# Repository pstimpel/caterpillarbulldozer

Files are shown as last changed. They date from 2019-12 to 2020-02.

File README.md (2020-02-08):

# Caterpillar bulldozer
3D printed radio controlled bulldozer, 2 feet long

License: https://creativecommons.org/licenses/by-nc-sa/4.0/

Most obvious limits of this license:
- You are not allowed to use this stuff for commercial purposes
- You can download, reupload and change the stuff, but have to release it under the same license again
- You have the mention the origin, "Original by Peter Stimpel, https://github.com/pstimpel/caterpillarbulldozer/"

## Home of this project

https://github.com/pstimpel/caterpillarbulldozer/

### Other ressources

- Thingiverse: https://www.thingiverse.com/thing:4057714
- Prusaprinters.org: https://www.prusaprinters.org/prints/15078-caterpillar-bulldozer-rc
- Pinshape: https://pinshape.com/items/57510-3d-printed-caterpillar-bulldozer-rc

IMAGE ALT TEXT HERE (https://www.youtube.com/watch?v=pU6fe7RiBuI)

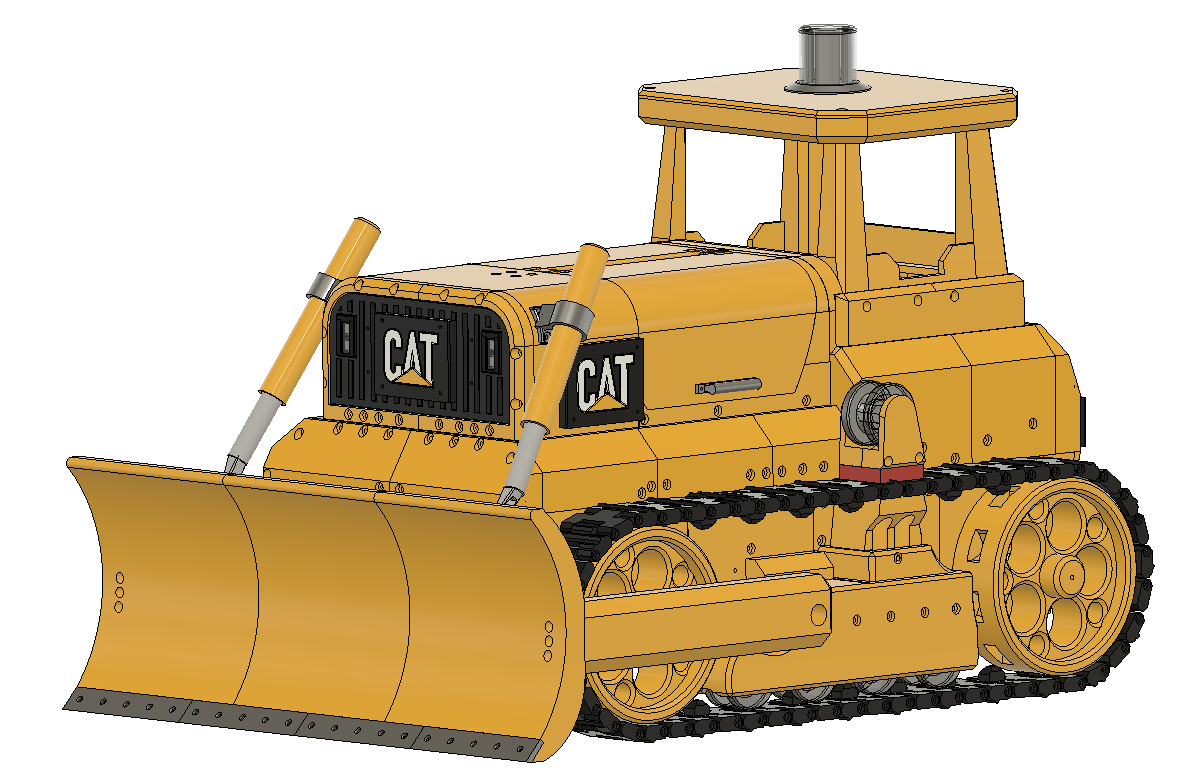
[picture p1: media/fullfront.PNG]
In all its glory


**Table of contents**
* [What's the story?](#what-s-the-story-)
* [A bulldozer!](#a-bulldozer-)
* [Sourcing parts, what do we need](#sourcing-parts--what-do-we-need)
+ [Filament, print instructions](#filament--print-instructions)
+ [Candy](#candy)
+ [Bearings](#bearings)
+ [Screws, nuts and bolts](#screws--nuts-and-bolts)
    - [M2](#m2)
    - [M3](#m3)
    - [M4](#m4)
+ [Electronics](#electronics)
    - [RC stuff](#rc-stuff)
    - [stuff for lights and buzzer](#stuff-for-lights-and-buzzer)
    * [Stuff to create a pcb](#stuff-to-create-a-pcb)
* [Let's build the bullozer now](#let-s-build-the-bullozer-now)
* [Who to thank?](#who-to-thank-)
* [Donation](#donation)
* [Feedback](#feedback)

## What's the story?

I run my hobby 3d printing for more than a year now. Yes, I am a noob. Along the way I looked for a software to do my CAD, and found Fusion 360 from Autodesk. So, I had to learn Fusion. Youtube offers great ressources, most important there is the Fusion 360 channel run by Autodesk (https://www.youtube.com/user/AutodeskFusion360). There is a bunch of lovely people with their tips and tricks - more details at the end of this. 

However, one day - I was finishing my illuminated death star (https://www.prusaprinters.org/prints/5661-death-star-illuminated-mood-lamp-death-star ), I was looking for a thing taking more than a few days to create. Something to be my project for the winter. And, I was keen to create something running on tracks. Now I dislike building replicas of war machinery, so a tank was no solution to me. 

## A bulldozer!

I was using my favorite search engine duck duck go, and found Caterpillar to be a big brand in the bulldozer manufacturers community. I sat down and thought what to do, and came up with these topics:

- no real replica, more a free style model of a bulldozer
- dimensions? who cares!
- radio controlled, and not steered by a gearbox, but two motors (I liked the challenge of learning how to program my radio control)
- the blade at the front should move up and down by servo motors

But how the f*** could I achieve these goals? I decided to create a gearbox first, add the motors to a motor stand, so I could test if running two independent tracks by an own motor each would be a cool thing. 

And what to tell: doing gears is easy enough in Fusion. I added some bearings, adjusted the tolerances, and had a working gearbox a few hours later. I mirrored it, added some dirty housing around, and created a design for the tracks.

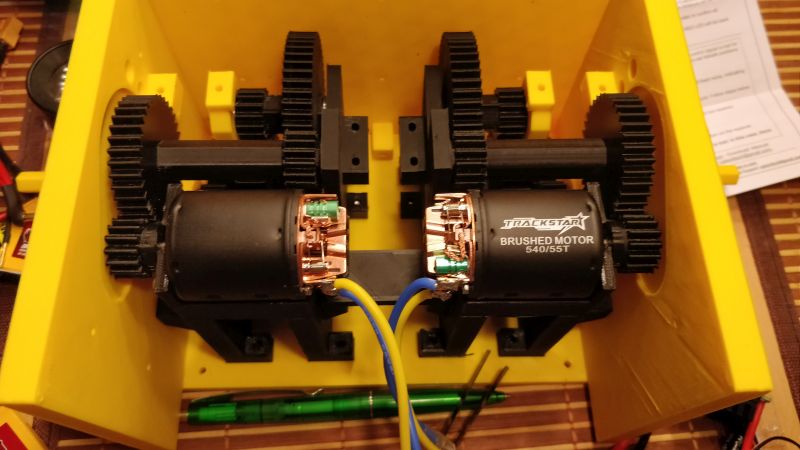
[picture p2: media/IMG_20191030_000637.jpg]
First revision of the gearbox


Stearing two tracks having a motor each was not as easy as I thought. But the guys at (https://openrcforums.com) helped me out, so I got my radio control running quite soon. 

Next step: tracks. I designed a track in Fusion, printed the parts, screwed it together and started a very first test. This was the beginning of this story.

Video of the first test: 

IMAGE ALT TEXT HERE (https://www.youtube.com/watch?v=s0oiE-nRtp8)

Now, how to go on? Usually, you would design all the stuff, and once you are happy with your CAD, you print and assemble the stuff. I was going a different way. I designed the stuff during building the vehicle. Step by step both the CAD and the vehicle evolved. This caused some major mistakes and lot's of fun at the same time. I love it that way - CHAOS! One thing that was quite tough: you had to think about the next step, one step ahead, so you can connect the two steps somehow. Thank the lord there is candy ...

## Sourcing parts, what do we need

We need a 3d printer. I was using my Prusa I3 MK3. It has a build plate of 200x250, and Z is 200+. Some parts make use of these dimensions. If your printer has less build area, this project might not be for you, or you need to cut things apart. Of course we need tools. And, we need ...

### Filament, print instructions

I was using filament from my favorite supplier https://dasfilament.de. The print is PLA only, so I ordered about

- 6 spools yellow
- 1 spool transparent
- 2 spools black
- 1 spool anthracite
- 1 spool silver
- 1 spool white

Numbers are valid for printing in 0.3 layer height, using 3 shells horizontally and vertically, 10% cubic infill (except the gears and axles, I used 50% cubic infill here).

I was taking care not to need any support. I achieved this goal, except for very few parts.

The stls are not in their orientation for hassle free printing, I'm sorry. You do need to make this yourself in your slicer.

**Update upon user request**: If you find 3mf files to be more convinient to print, you might want to look at the folder "3mf-200x250". It contains 59 3mf-files. The orientation of the parts to print is set there already, also the numbers of parts to print is the right one already. To use these files your slicer has to support 3mf. Each of these files contains a full organized print bed, made for print beds equal to or larger than 200x250mm in dimension. Each filename is led by a number, which represents the order you should print the files. It contains as well an information for the filament color to use. "nocolor" means you can use a color of your choice since the files are hidden inside your bulldozer. 

### Candy

The build will take some time, not to talk about the 200 hours of printing. This means, it will be nerve-wracking :). Get some good stock of candy to please yourself once you enter mentally strange situations. I can tell you: you will need it!

### Bearings

We need 40 bearings of type 6700ZZ. Dimensions are 10x15x4mm. These are standard bearings, you should find them very easy. I ordered mine from https://www.kugellager-express.de/. 

We need another 12 bearings of type 6904 with dimensions 20x37x9mm. I ordered them from the same supplier.

### Screws, nuts and bolts

I order my stuff from a shop called https://www.schrauben-paul.com/. All given dimensions are mm. I did not count each single screw, so all numbers are estimates. However, if you enter such a project I expect you won't order exact counts.

#### M2
- 50 M2x8, cylinder head
- 50 M2x10, cylinder head
- 50 M2x16, cylinder head

#### M3
- 4 scrubscrews M3x6
- 4 square nuts M3
- 100 M3x10, cylinder head
- 100 M3x14, cylinder head
- 300 M3x20, cylinder head
- 100 M3x25, cylinder head
- 200 M3x45, cylinder head

#### M4
- 4 Bolts 40mm

### Electronics

I expect you have a radio control already. Therefore I do not link a receiver. But, you will need one 8 channel receiver matching your radio control and local laws. If you skip the lights part, a 4 channel receiver will do. As well, all my builds are ran by 2S Lipo, which means the voltage of the linked components below does match this battery type. If you go for a different voltage, please select your components in a way the match together.

#### RC stuff
- 2 standard servos, metal gear, metal servo arm (https://www.amazon.de/gp/product/B0716V3WNH/)
- 2 motors type 540, 55 turns or similar (https://hobbyking.com/de_de/1-10-540-carbon-brushed-motor-55t.html)
- 2 ESCs (https://hobbyking.com/de_de/hobbyking-x-car-45a-brushed-car-esc.html)
- 2 Lipo 2S, like (https://hobbyking.com/de_de/turnigy-nano-tech-shorty-4200mah-2s2p-65-130c-hardcase-lipo-pack-roar-approved.html)
- 2 connectors to connect your Lipos and ESCs

#### stuff for lights and buzzer
- Arduino Nano 5 Volt
- Resistor 0.25W 270 Ohm
- Buzzer 5 Volt (https://www.amazon.de/gp/product/B073RH8TQK/), we need the bigger one out of the package
- 1 switch like in (https://www.amazon.de/gp/product/B07MY2WVQ3)
- RGB leds (https://www.amazon.de/gp/product/B01N97A0XG)
- 3 cables for connecting receiver and Arduino, servo cables like (https://hobbyking.com/de_de/twisted-15cm-female-to-female-servo-lead-jr-22awg-10pcs-set.html)
- wires to connect the LEDs (https://www.amazon.de/gp/product/B01BI1G88C)
- 12 pin headers
- solder stuff, some shrinking tube 3mm

##### Stuff to create a pcb

We create a one sided, 60x60mm pcb. I expect you either have the stuff to do that because you know how to do it, or you just order the pcb from your favorite supplier. You can skip the pcb part completely, because it just controls the lights and the buzzer. If you do not need this, just order the rc stuff only. You could exchange your 8 channel receiver for a 4 channel receiver in this case as well.

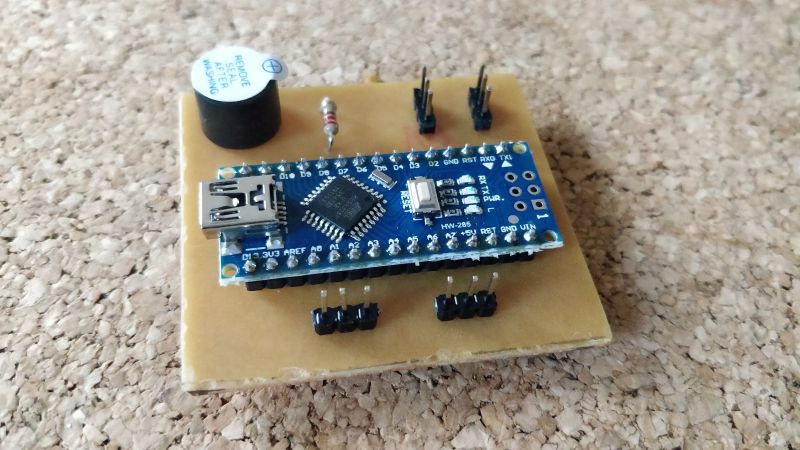
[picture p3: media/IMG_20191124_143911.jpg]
Arduino board


But hey, no lights? Really?

**Warning**: I have still issues with flickering, randomly color changing LEDs, seems there is some noise coming from the ESCs and I need to filter those out. It is very likely the pcb design and parts list of the pcb will change soon.

## Let's build the bullozer now

**Remark**: if not mentioned any different, we talk about screwing things together using M3 screws. Just screw them into the plastic parts, make sure not going to fast when screwing them in. Friction causes heat, and heat cause melted plastic parts. Just be gentle. Do not overtighten the screws, there is no need for it. It is on you to determine the right length of a srew, just use common sense and do not try to mount a small handle using M3x45. 

We start with the gear box. Print all items in subfolder "BothSides" twice. Print items in "Housing", "LeftOnly" and "RightOnly" once each. The gears and axles need to be stable. I suggest you to print the axles horizontally aligned. Use some more dense infill on the gears and axles. 

Mount the motorstands to the base. Assemble all axle-gear combinations twice, once for left and one for right gearbox. Take note of the indexed axles, and their counterpart gears. Most gears have one side flat, while the other has kind of a builtin spacer. The spacer side points outside the axle, to the bearing. Axles A, B and C provide spacer parts, which sit in the middle between the gears.

Axle A is the one right after the motor. Axle B "connects" to Axle A and Axle C and so on. Should be straight forward. Do not miss the 6700 bearings, one at each end of each axle. Except "rearaxle", we will take care of those later.

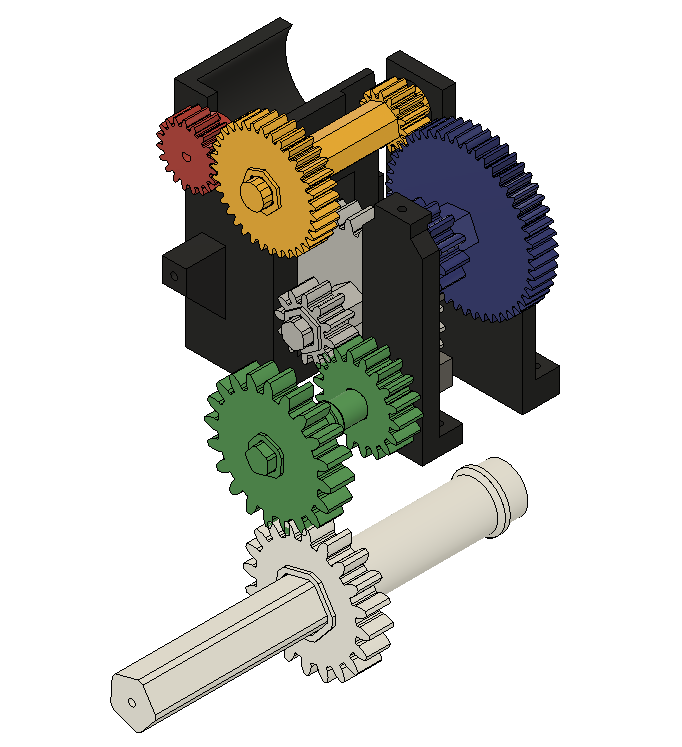
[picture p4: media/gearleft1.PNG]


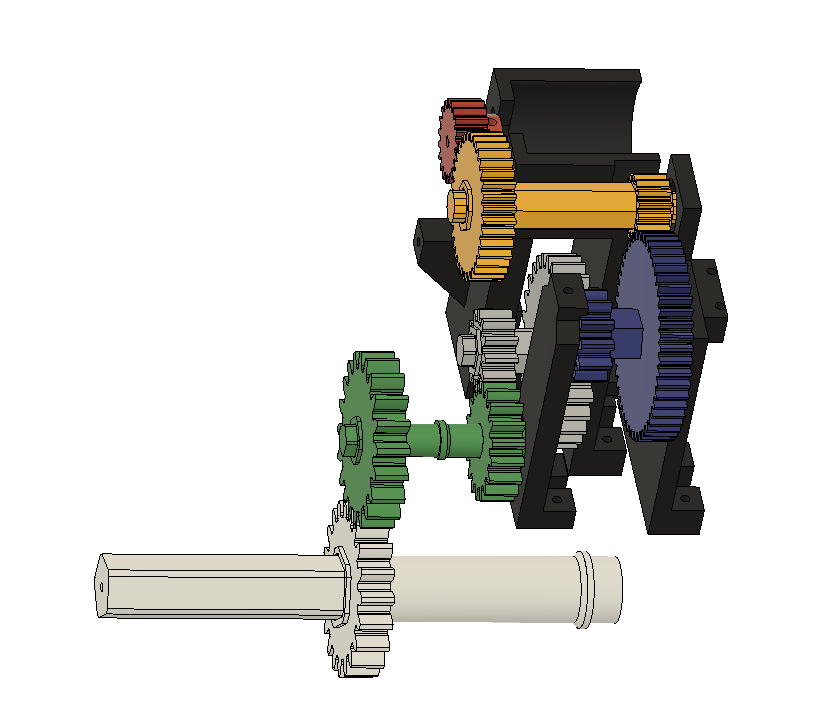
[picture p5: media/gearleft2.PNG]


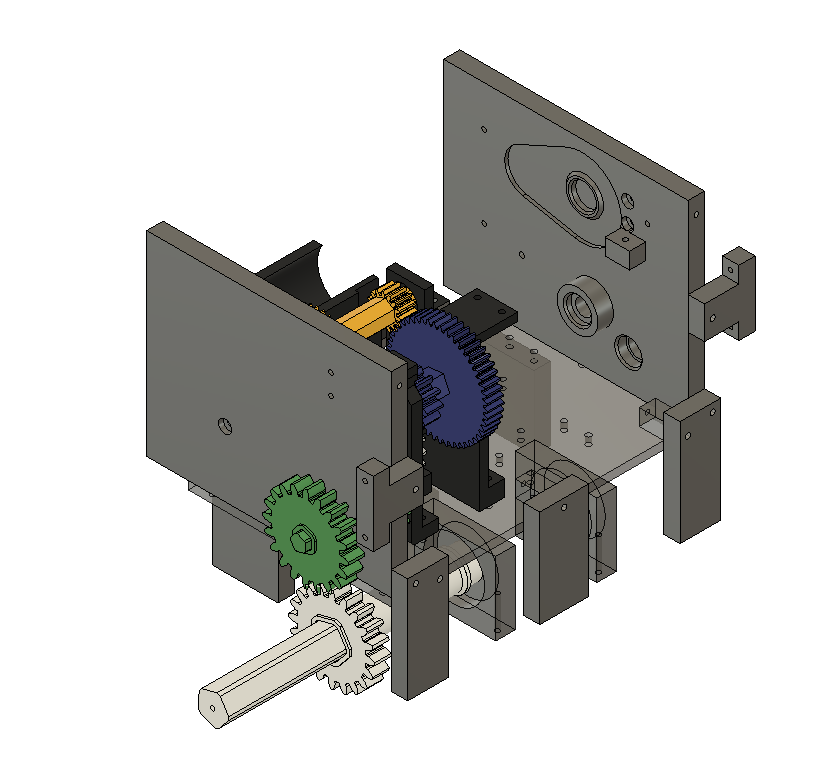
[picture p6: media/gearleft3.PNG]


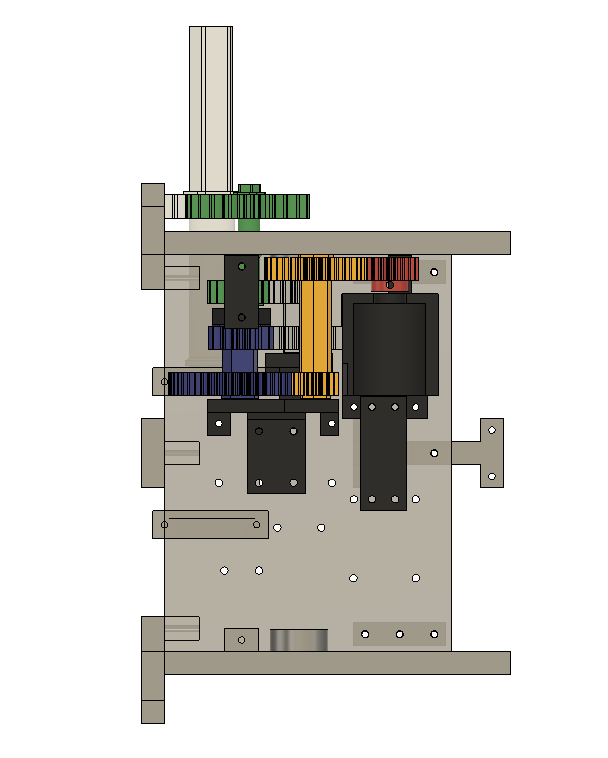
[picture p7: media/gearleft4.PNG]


Once all axles are assemnbled, use the "Gearboxbearingstands" to mount them at your gearbox base. Do this twice, for left and right gearset. Mount the outer housing "Gearhousing left/right". Make sure the gears can spin freely. Add the motors to the stands, fix them. The pinions are now mounted to your motors using 4 squarenuts and 4 scrubscrews M3. Add the supports and connector parts for Bearing holders and motorstands.

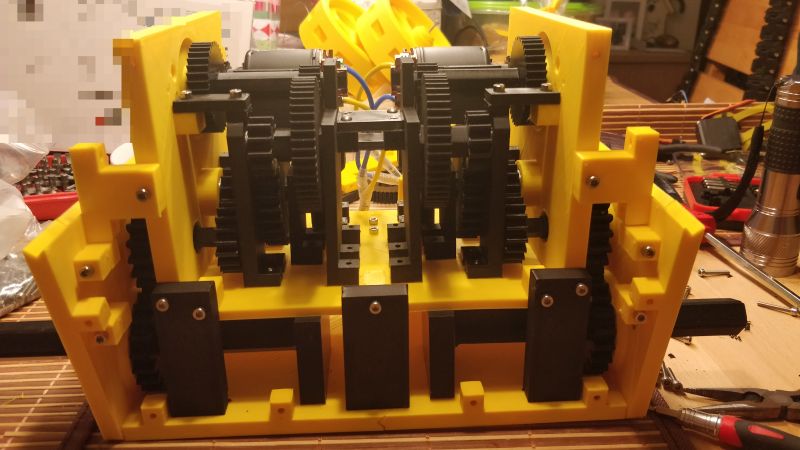
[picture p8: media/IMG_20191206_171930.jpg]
The gearbox, ready assembled and mounted to the chassis of the vehicle


This is a good time to connect ESCs to the motors, Lipos to the ESCs and the receiver to the ESCs - for a very first test. **WARNING: Remove one of the positive voltage pins of your ESC before connecting them to your receiver**. This is **IMPORTANT**! If you miss this, **BLUE SMOKE** might appear out of your receiver and/or your ESCs. Bind the receiver to your radio control. I am using a mode 2 controller. My setup is like:

Channel 1 connected to left motor/esc, channel 2 connected to right motor/esc

* CH1 100 RUD * 100 ELE + 100 ELE
* CH2 -100 RUD * 100 ELE + 100 ELE

Check this out for more info (https://openrcforums.com/forum/viewtopic.php?f=5&t=12296), and kudos to the helpful gents over there.

And while we are at it, set CH 3 and CH6 both to P1, which will do the blade servo control.  

On top, set CH4 bound to ELE, and CH5 to RUD. CH4 and CH5 will connect to our Arduino for controling the LEDs and buzzer. If you dislike going for lights and buzzer, you can skip this last step completely. 

**Important**: Write down how you connected your ESCs to witch motor. If you push "forward", both axles have to turn forwards. If not, switch the connection between motor and ESC. Now push "forward" and "left". The left axle should go slower or stop completely, while the right axle turns forward. If it is the other way, just flip ESCs and restart this test. If you push backwards and left, the left axle should stop again, while the right axle turns backward. Check what happens if you "turn right". Do not go any further until you finished all this with a success!

Now print all parts from "LowerChassis". Print "InnerSupportLeft" and "InnerSupportRight" twice each. The numbers are ordered from front to back. Mount your assembled gearbox to the bottom using the support pieces. Use "InnerSupport..." to keep the bottom parts together. Add the rearaxles and their bearingholders. Do not forget to add the bearings of type 6904, 2 on each axle. Add the 6700 bearings to the outer end of both Axles "D", and the "Gear2AxleD-5edges" as well. Mount the "LowerChassis..." parts left and right. These keep all the other parts and axles in place. Add stability by making use of "InnerSupportLeft" and "InnerSupportRight".

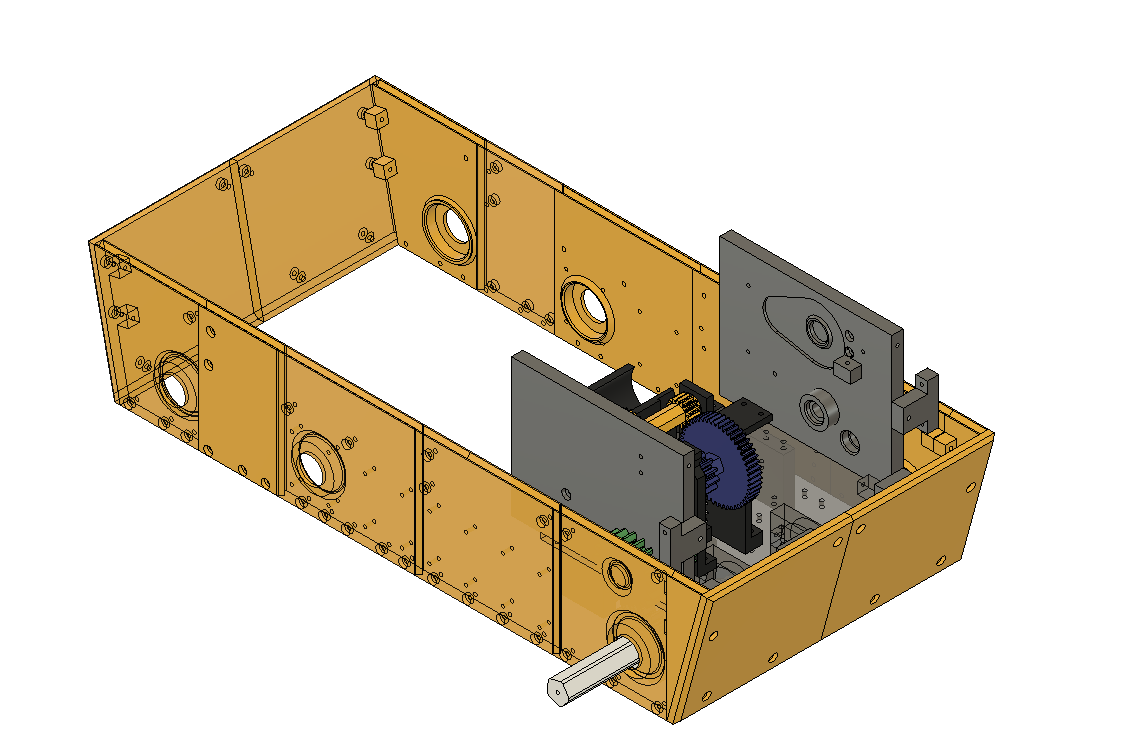
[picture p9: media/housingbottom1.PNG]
Lower Chassis 1


It is printing time again: we print all the stuff from "Blade", "Drive" and "Tracksupport".

Print all parts once, except:

twice: BladeBarAxle, BladeHydraulicsBolt, BladeHydraulicsClamp, BladeHydraulicsTube. BladeServoBar, BladeServoLever, FrontAxle, FrontAxleDistancekeeper, UpperSupportAxle

four times: BladeServoLock, Wheel, UpperSupportSpacer, UpperSupportWheel

eight times: LowerSupportAxle

16 times: LowerSupportSpacer, LowerSupportWheel

52 times: ChainA, ChainB

Insert 6904 bearings into "BladeBarBearingHolder". Combine "BladeBarAxle" and "BladeBarLever", add 6904 bearings. Mount Axles using "BladeBarBearingHolder" Left/Right to the bottom. 

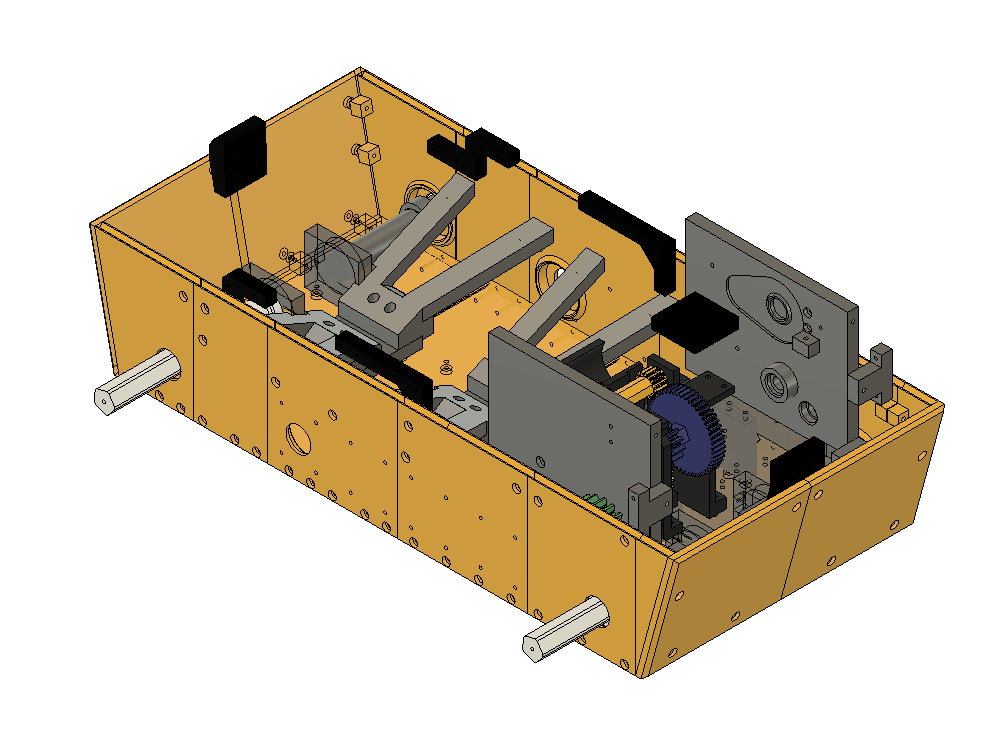
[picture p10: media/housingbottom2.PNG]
Lower Chassis 2


Add a 6904 bearing to the round end of the "FrontAxle". Add one "FrontaxleDistancekeeper" to the long side. Add a 6904 bearing to the longside. Mount it using the "FrontaxleBearingHolder". Do that twice for each side.

Now let's do the track supports. Mount two "LowerSupportWheel" at one "LowerSupportAxle", and put one "LowerSupportSpacer" on each end. Add a 6700 bearing at each end of the axle. Do this procedure eight times.

Mount two "UpperSupportWheel" at one "UpperSupportAxle", and put one "UpperSupportSpacer" on each end. Do this procedure twice.

Mount "TracksupportInnerLeft" to your chassis. Insert four of your "LowerSupportAxle" builds. Add "TracksupportOuterLeft" to your vehicle. Repeat this step at the right side using "TracksupportInnerRight" and "TracksupportOuterRight".

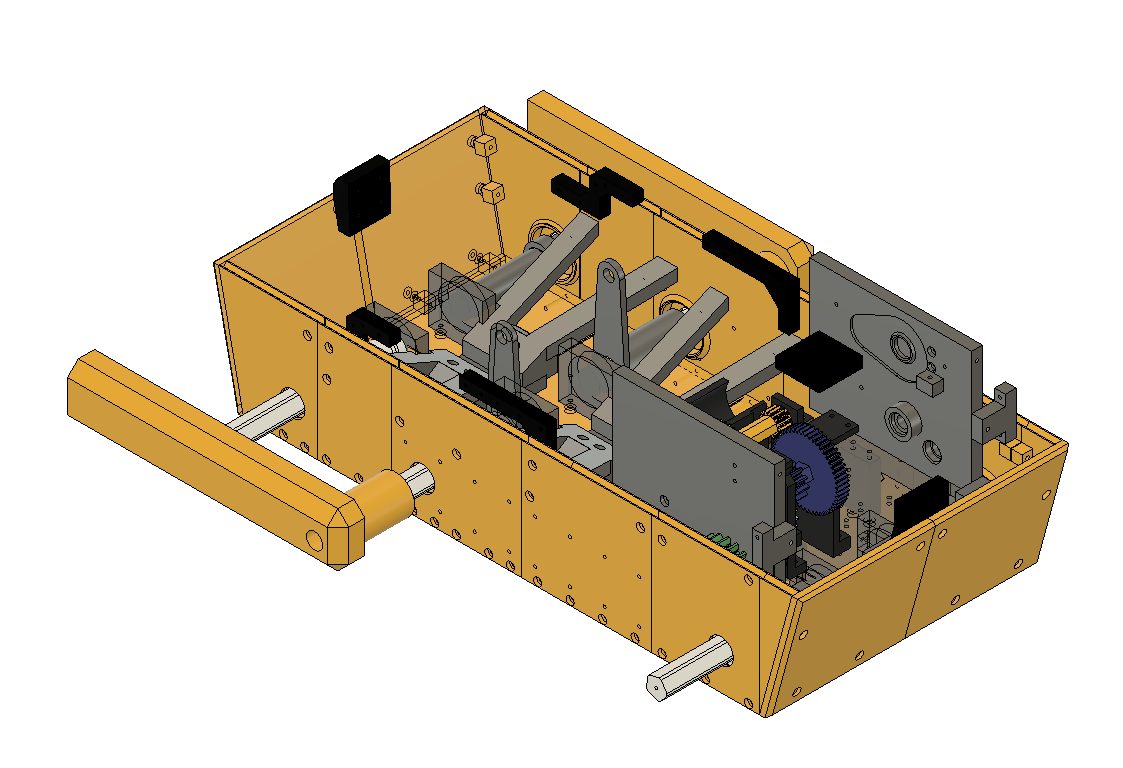
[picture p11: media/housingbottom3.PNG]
Lower Chassis 3


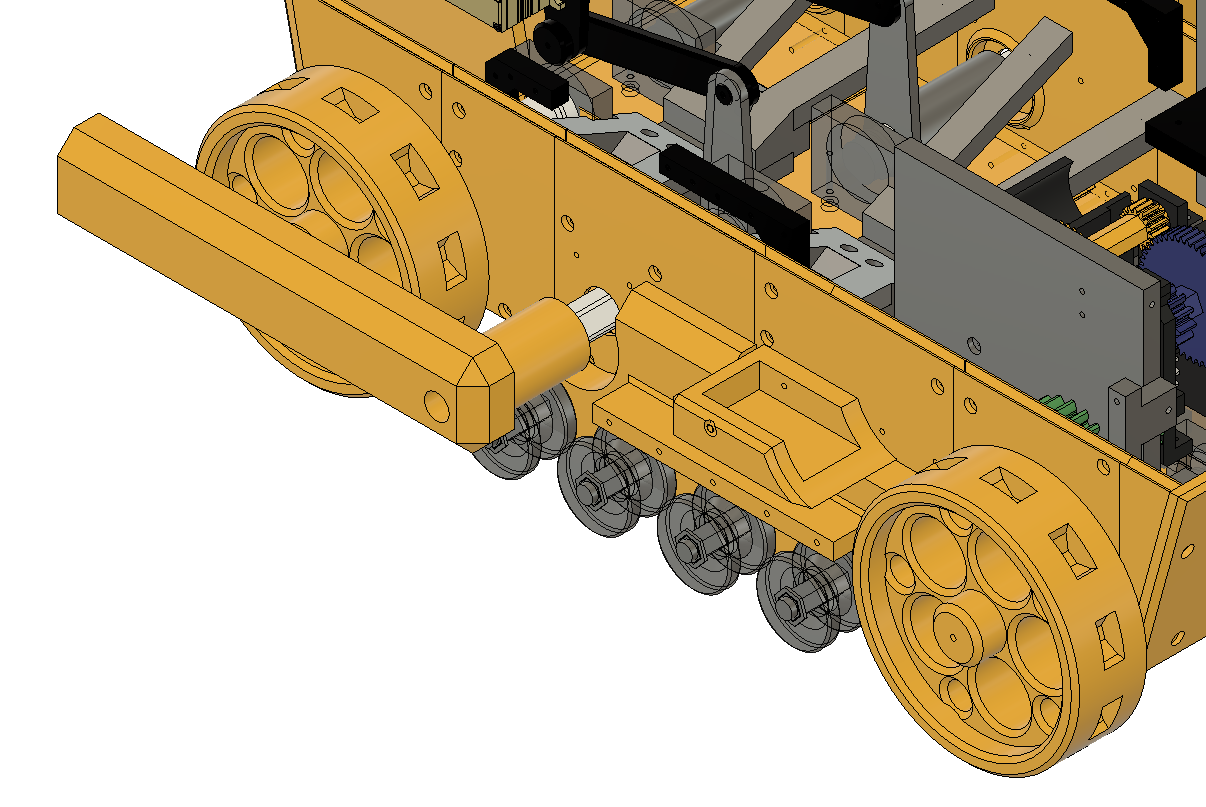
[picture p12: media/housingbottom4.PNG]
Lower Chassis 4


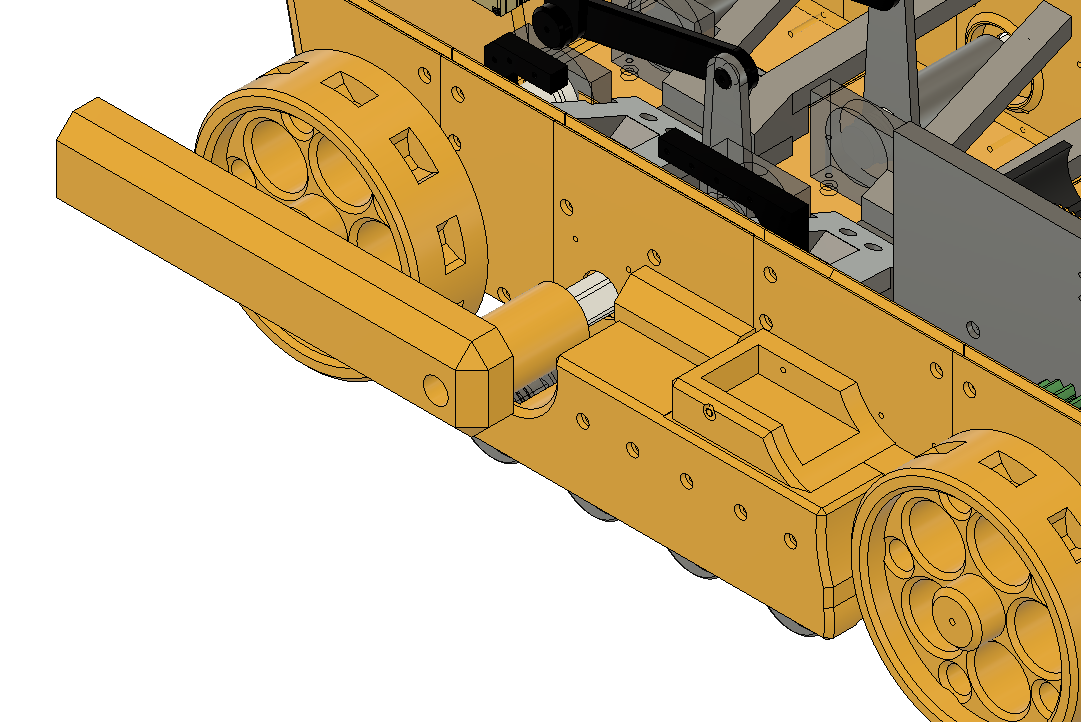
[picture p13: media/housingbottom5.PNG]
Lower Chassis 5


Starts to look serious, right?

Mount "TensionmountLeft" to your vehicle. Mount "TensionWheelholderInnerLeft", "TensionWheelholderOuterLeft", one of your "UpperSupportAxle" builds and "TensionBaseLeft". Mount this assembly to "TensionmountLeft" using a M3x45 screw.

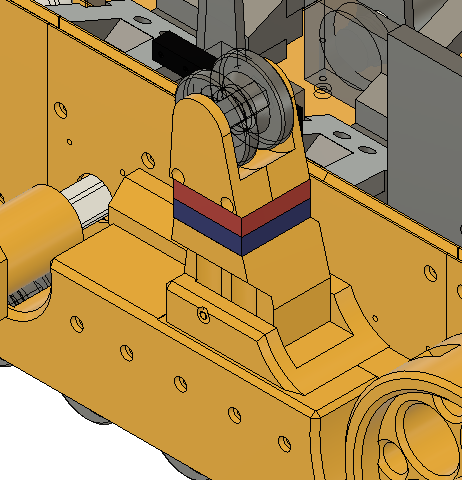
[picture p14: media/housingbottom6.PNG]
Lower Chassis 6


Repeat this step for the right side of your vehicle.

Add the 4 wheels to your axles. Secure the wheels using M3#20 screws.

Time to build the tracks. We build two of them. So, 26 "ChainA" and 26 "ChainB" create one track, screwed together by 52 screws M3x45. The horn of "ChainA" points to the inside of our track loop, while the 3 edges of "ChainB" point to the outside. We screw the left track from the left side of the track, while we screw the right track from the right side. This will make it much easier to replace broken chain parts later on. Again, be careful with applying forces and heat out of friction. Depending on your screws they might have a non threaded part below the cylinder head. If so, use a 3.5mm drill to widen the holes of your chain parts, only the ones pointing away from your vehicle - the ones you start screwing in. Do not change the diameter of the holes the thread of your screw goes into. 

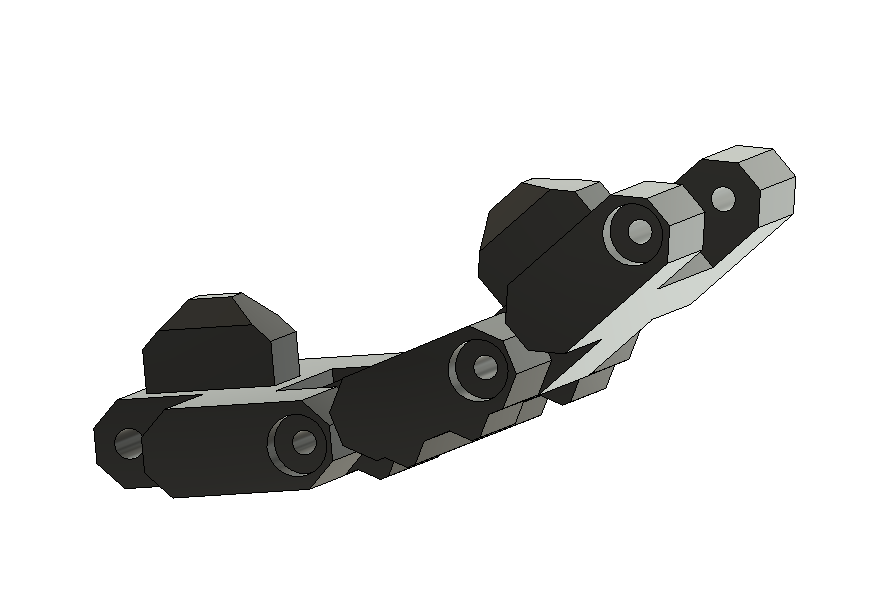
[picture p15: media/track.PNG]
Tracks


Great job, you have 2 tracks now. Mount the left one to the left side, the right one to the right side. Could be you need to lose your tension mechanisms again to make the tracks fit. There is a so called "TensionBlock" in the package "Tracksuppport". If your track is too lose, just mount one between "TensionBase" and the supportwheel assembly. Warning: do not tension your tracks like belts on your printer. They need to have some wiggle room. In case of doubts leave the "TensionBlock" away from your assembly.

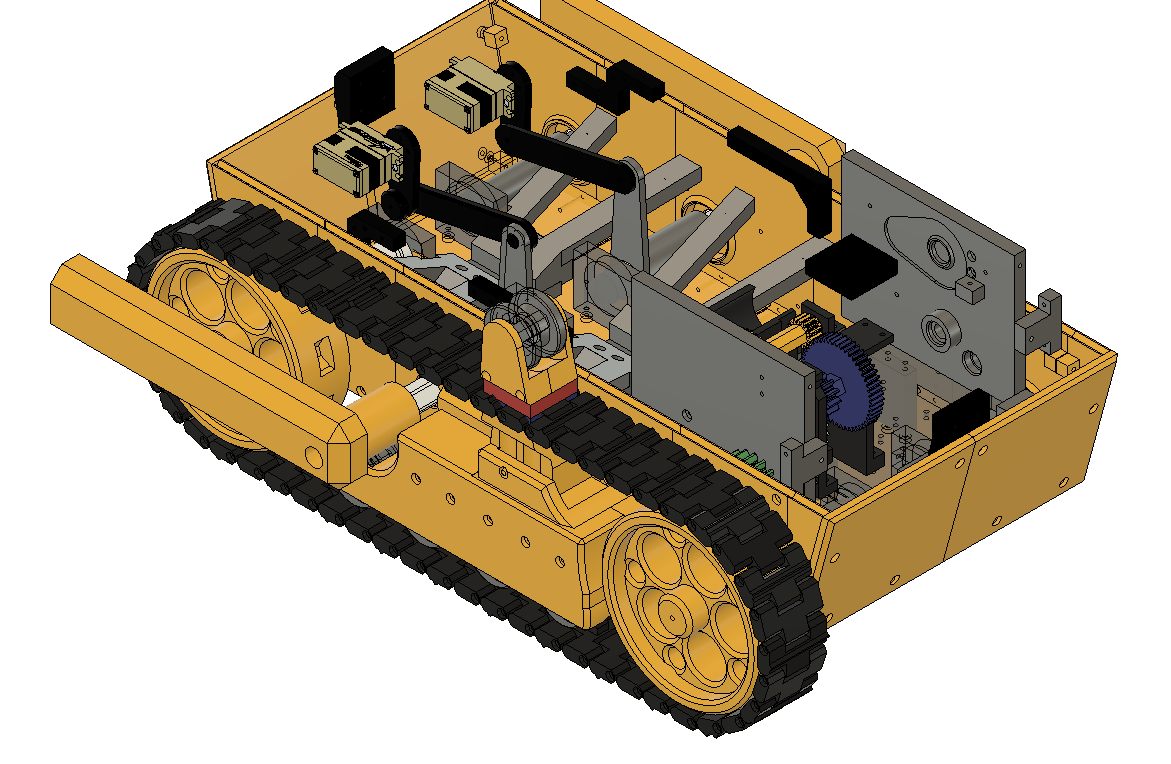
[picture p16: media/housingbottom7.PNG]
Lower Chassis 7


If you like, this is the right time for a break. You could eat some candy, or drive around with your vehicle. Basic forward/backward and steering will work already. 

OK, let's move on. You will need to print the content of "UpperChassis" and "Grill". Mount all the "UpperChassisLeft/Right" parts using the support parts of that package. Parts 4 and 5 are connected directly to each other. Mount both servos to the servo mount. The servohead should point to the right side, backwards. Mount this assemblies to the upper chassis. Now mount the "BonnetSupport" parts on top of the upper chassis. Mount the CAT Logo and the Tailgate as well to the back.

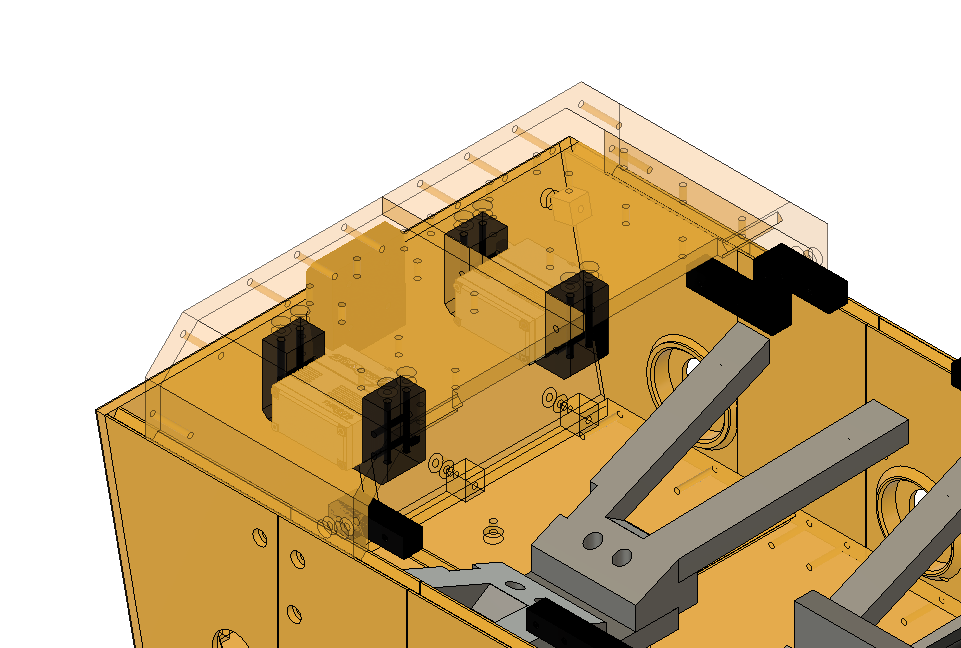
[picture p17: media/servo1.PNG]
Servo


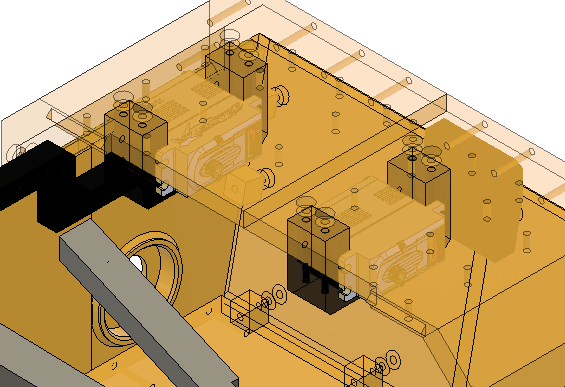
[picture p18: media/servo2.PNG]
Servo


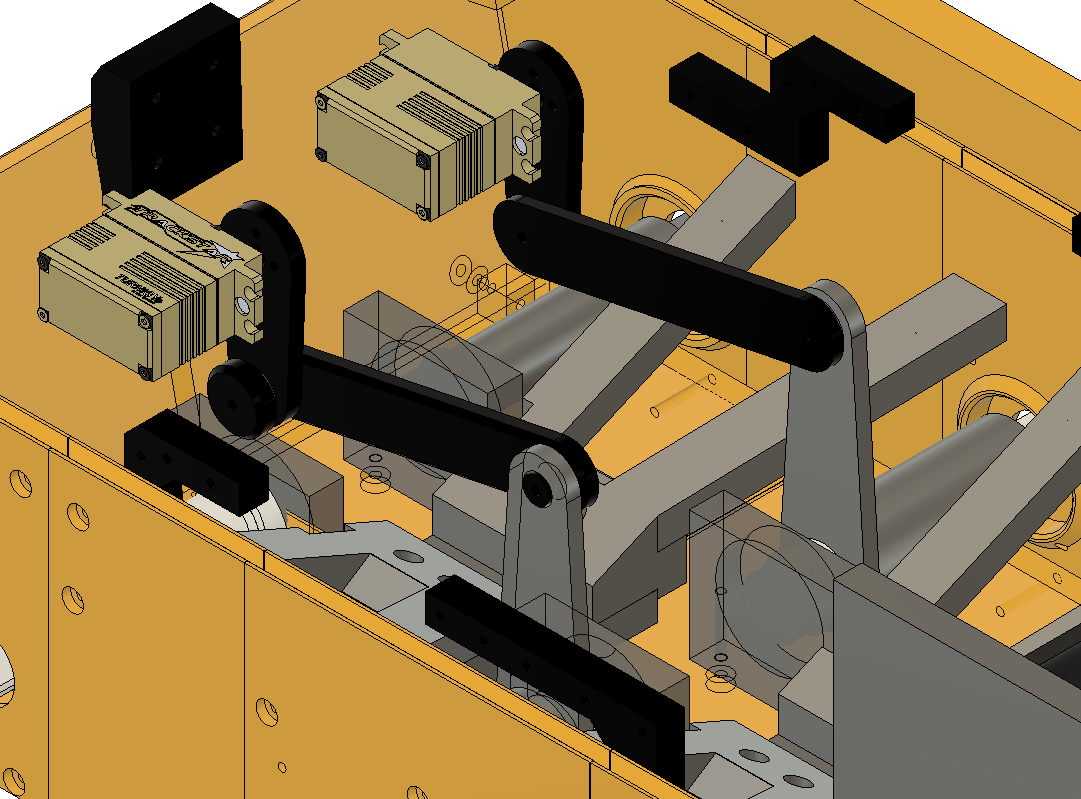
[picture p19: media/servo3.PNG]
Servo


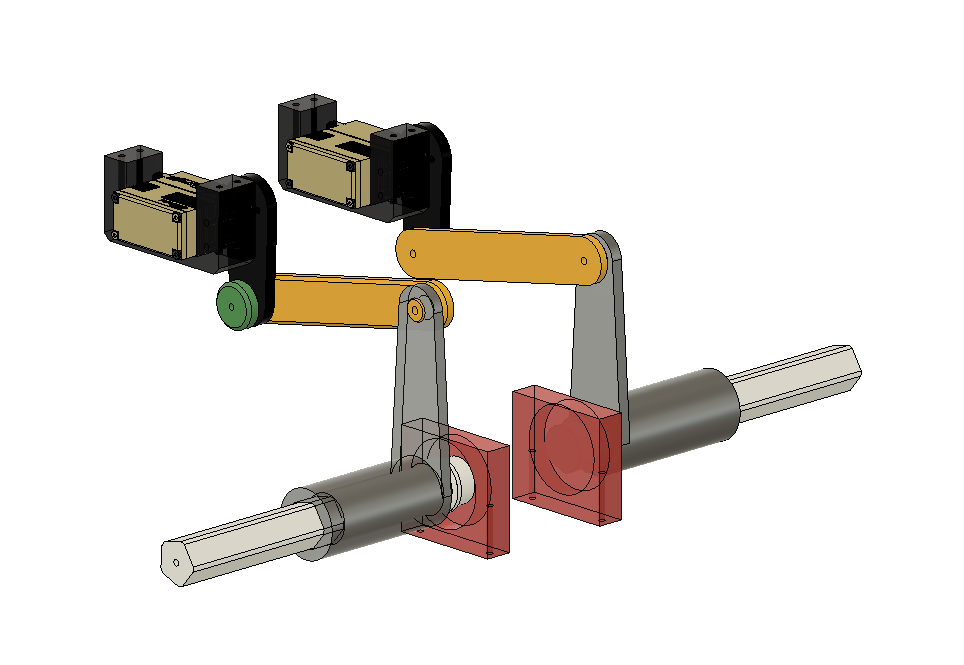
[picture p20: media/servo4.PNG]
Servo


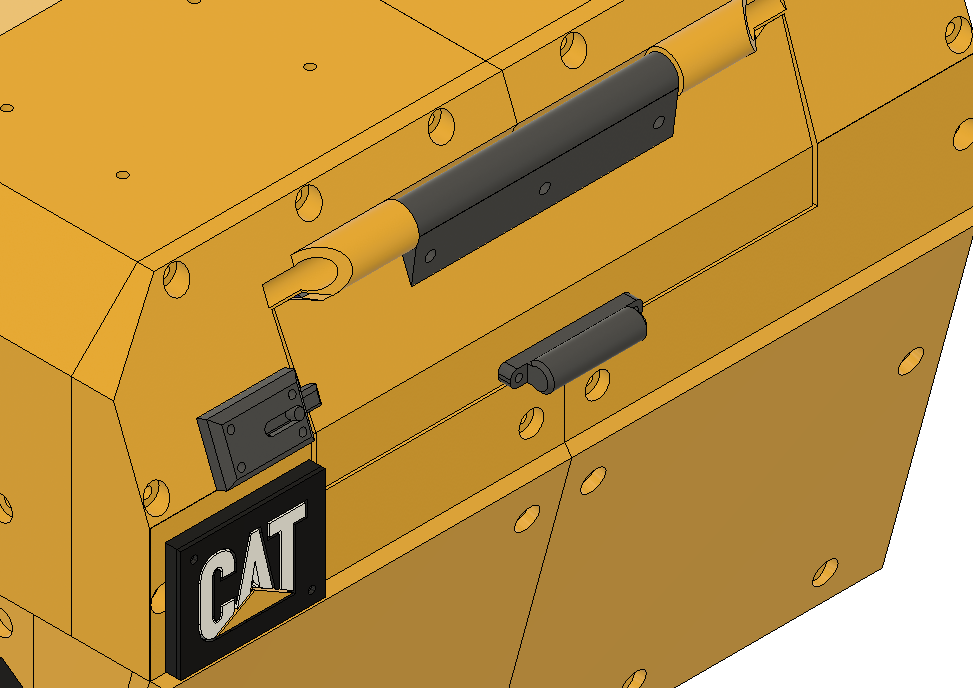
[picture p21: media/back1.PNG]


Mount the round shaped servo head to the servos. Mount the "Bladeservolever" to the servohead. Once finished, the lever should point straight downwards, at both servos. Mount the BladeServoBar to it, and lock it using 2 of the BladeServoLocks.

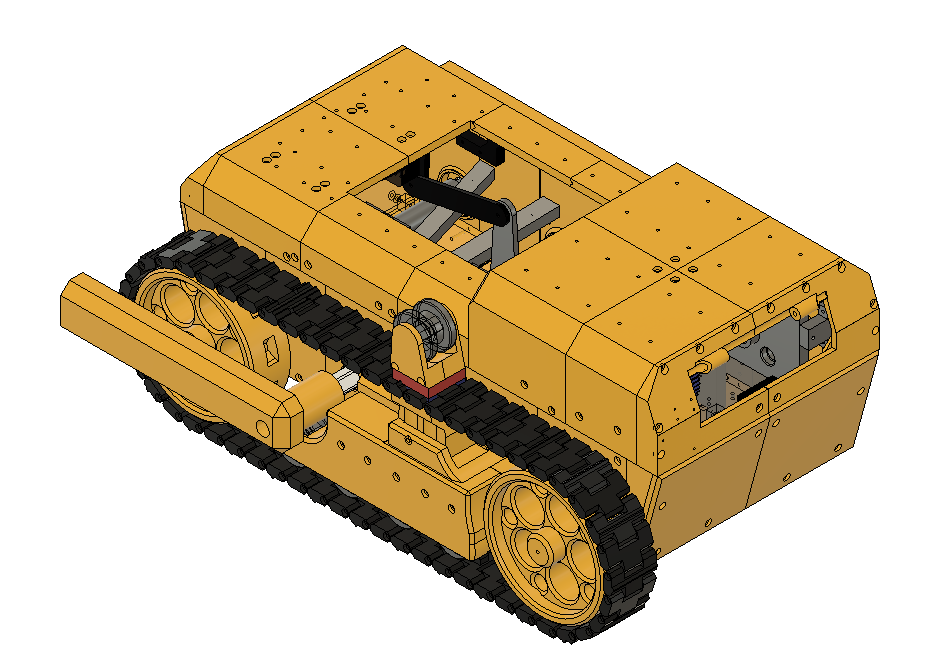
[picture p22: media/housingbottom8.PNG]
Lower Chassis 8


Mount the upper chassis assemby to your vehicle. Use the left support parts out of the UpperChassis package to do that. 

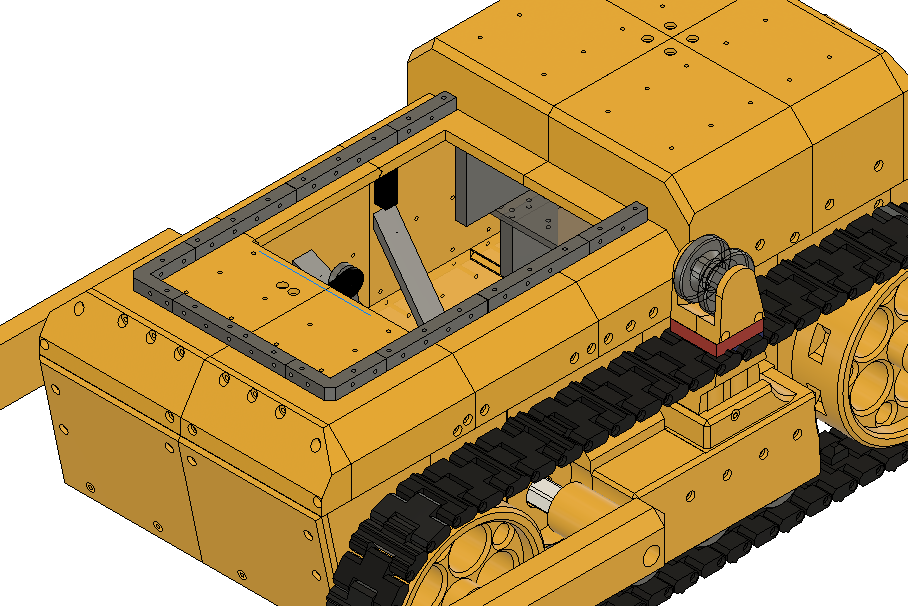
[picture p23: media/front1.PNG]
Front


Connect the BladeServoBar to its BladeBarLever, use the two remaining BladeServoLocks. I am sorry, but there is not much room to do that. You will make it. If not, remember your stock of candy, take a break, and try again. 

Time to assemble the grill. Print 4 sets of the LEDHousing package. Connect "GrillLeft", "GrillRight" and "GrillInsert". Add the CAT Logo to the "GrillInsert". 

If you go for the lights option: At this point you should have your pcb, equipped with the Arduino, pin headers, buzzer and resistor. Orientation of the board: you look at your Arduino, not the solder side of the PCB. USB of your Arduino is pointing to the left, the buzzer is top left. Connect CH4 of your receiver to the up right pin header. Connect CH5 to the pin header next left to the up right pin header. Cut the left servo cable in half. Use one half, solder the switch to the both outer pins, connect this to the lower left pin header of your PCB - the orientation of the connector does not matter. If you did it right, one pin header is left unconnected. Now, break 2 LEDs free of your LED "matrix", and do that 4 times. Take care of not confusing DIn and DOut direction. Connect the left servo cable half. Connect the black wire to ground on the DIn side of your leds. Connect the opposite wire to Voltage 5V. Connect the middle pin to Din. Now connect DOut of that LED with DIn of the next LED. Connect ground and 5V of both LEDs as well. Create 15cm long wires, my advice is to use 3 different colors. Connect these wires to the DOut, 5V and ground of LED 2. We go on with this scheme. Never ever confuse DIn, DOut, 5V and Ground. See the following scheme for wire lengths:

Servo plug -> 15 cm -> LED1 -> direct connection -> LED2 -> 15cm -> LED3 -> direct connection -> LED4 -> 65cm -> LED5 -> direct connection -> LED6 -> 40 cm -> LED7 -> direct connection -> LED8 -> 25 cm -> strobe lights assembly below.

Now we need to break free 4 sets of 3 LEDs in a row, each. 

Connect the 4 blocks of 3 LEDs each as you did above. Scheme:

25cm cable from your assembly above -> LED9 -> direct connection -> LED10  -> direct connection -> LED11 -> 5 cm  -> LED12 -> direct connection -> LED13  -> direct connection -> LED14 -> 5cm -> LED15 -> direct connection -> LED16  -> direct connection -> LED17 -> 5cm -> LED18 -> direct connection -> LED19  -> direct connection -> LED20

Remember the candy ...

The lower numbered LED stays at the bottom, the higher numbered LED at the top of each single led housing assembly. Use LEDCase, insert the first LED assembly, add LEDGlas to the front slot, and close this housing using 2 M2x6 screws. Insert the first LEDHouse in the right side of your Grill. Make sure the screws of your LEDHouse point upwards. Repeat this steps for the 2nd LEDHouse. Make sure the lower numbered LED stays at the bottom. Mount the LEDHouse into the left part of your grill. 

Connect the servo plug of the LED to the right bottom pin header of your pcb. Make sure the ground pin points to the right!

Mount the Grill to the Supports of your UpperChassis. 

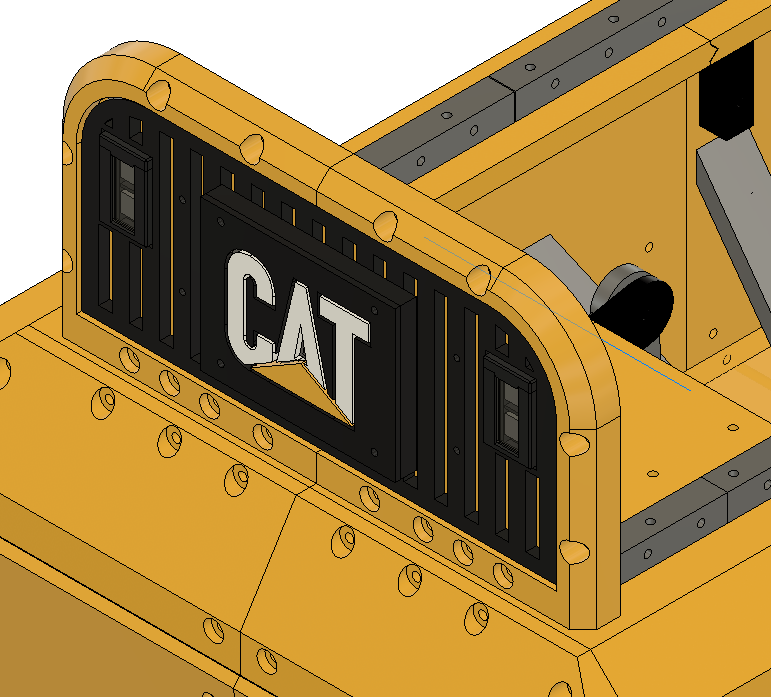
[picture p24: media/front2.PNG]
Front


Mount both ESCs to "ElectronicsESCBase", you can use double sided tape. Screw it in between the supports. Connect both ESCs to the motors, according to the scheme you created earlier when testing your gearbox. Connect the switches of the ESCs to "ElectronicsSwitchBase". Mount the buzzer switch as well. Screw the Switchbase into its place.

Mount both CAT logos to the "BonnetFront". Mount "Bonnetfront" to your Grill assembly. 

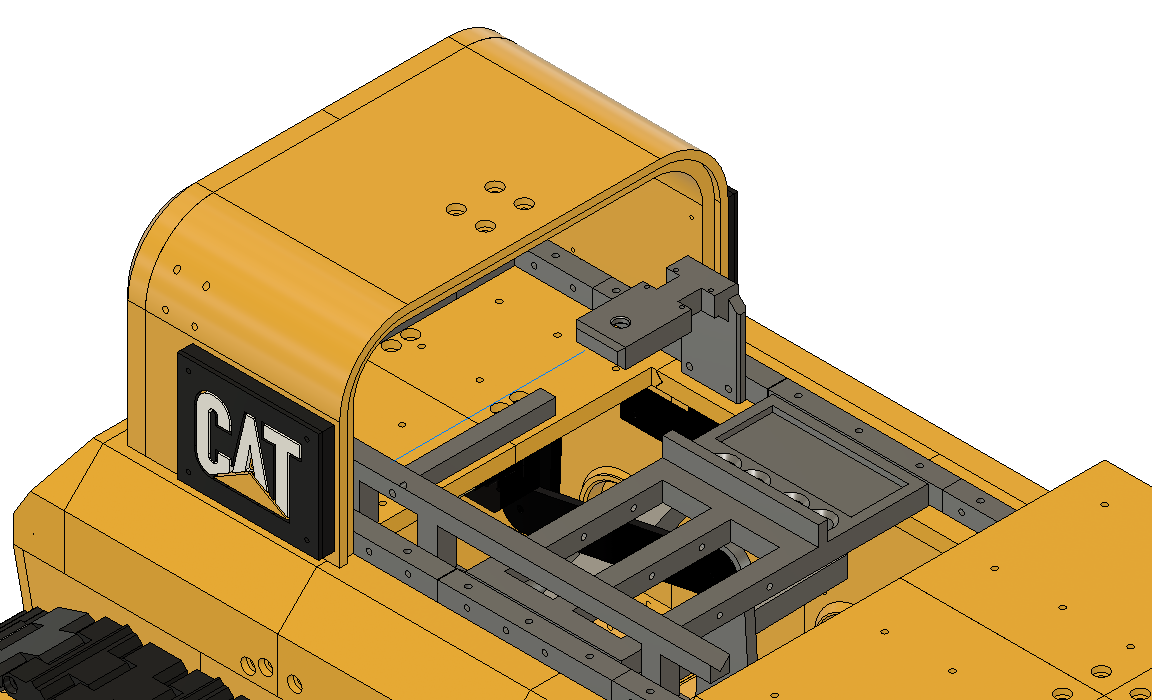
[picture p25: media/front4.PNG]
Front


Mount "ElectronicsCablechannel" and "ElectronicsBatteryBlocker", and mount this assembly to the left side of the UpperChassis supports. Use zipties to manage your cable stuff. The LED wire assembly goes straight to the back of your vehicle with the long cable you added between LEDs 4 and 5 (LED houses 2 and 3).

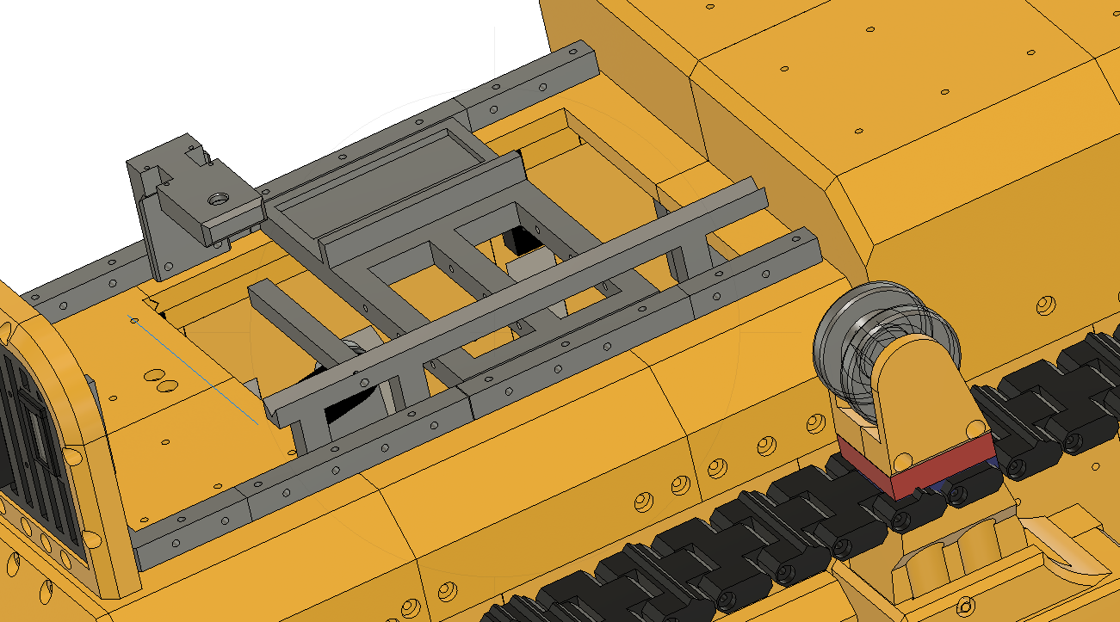
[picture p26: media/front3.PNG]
Front


Mount "BonnetBaseLeft", "BonnetBaseRight" and "BonnetBackbase" together. Mount it to your vehicle. 

Mount the "BonnetHandle" to "BonnetLeft" and "BonnetRight", using M2x8. Insert "BonnetLockBoltLeft" into "BonnetLockcaseLeft", and screw it to "BonnetLeft". Repeat this step for the "right" parts. Use M2x12 screws, and make sure the "Bolts" can move freely, towards the front of the vehicle. 

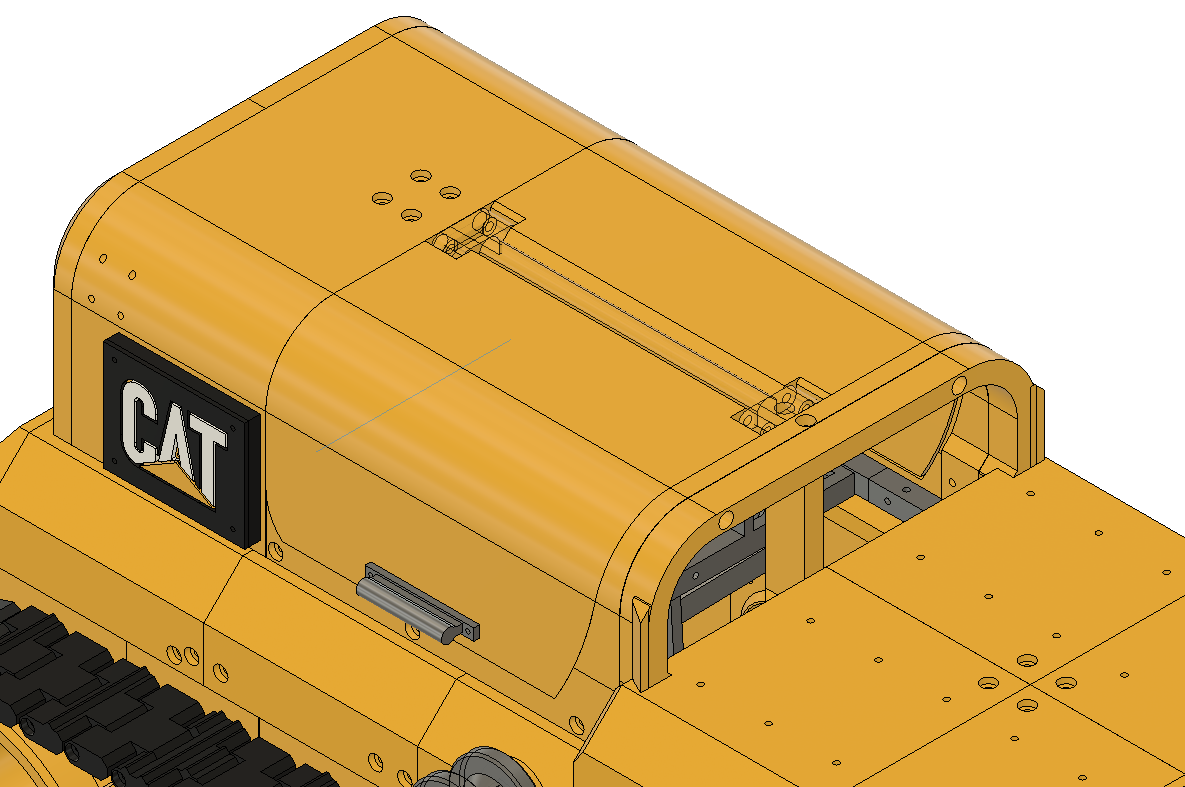
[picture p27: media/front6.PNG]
Front


Mount the Bonnets to the "BonnetHinge", mount the Hinge to the "BonnetHingeSupport". 

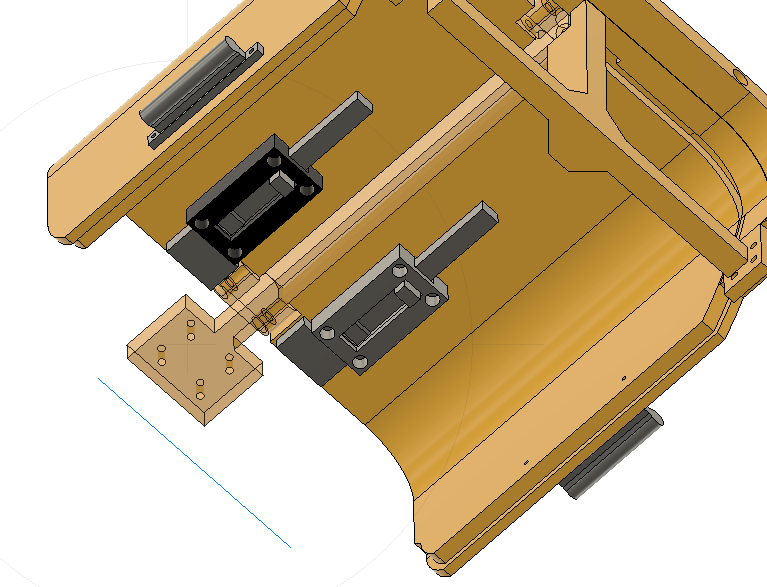
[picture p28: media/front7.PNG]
Front


Mount this assembly to the "BonnetFront" using 4 M3x14. 

Connect the "BonnetHingeSupport" and the "BonnetBackbase".

Mount "BonnetRear" at the end of the Bonnet stuff. 

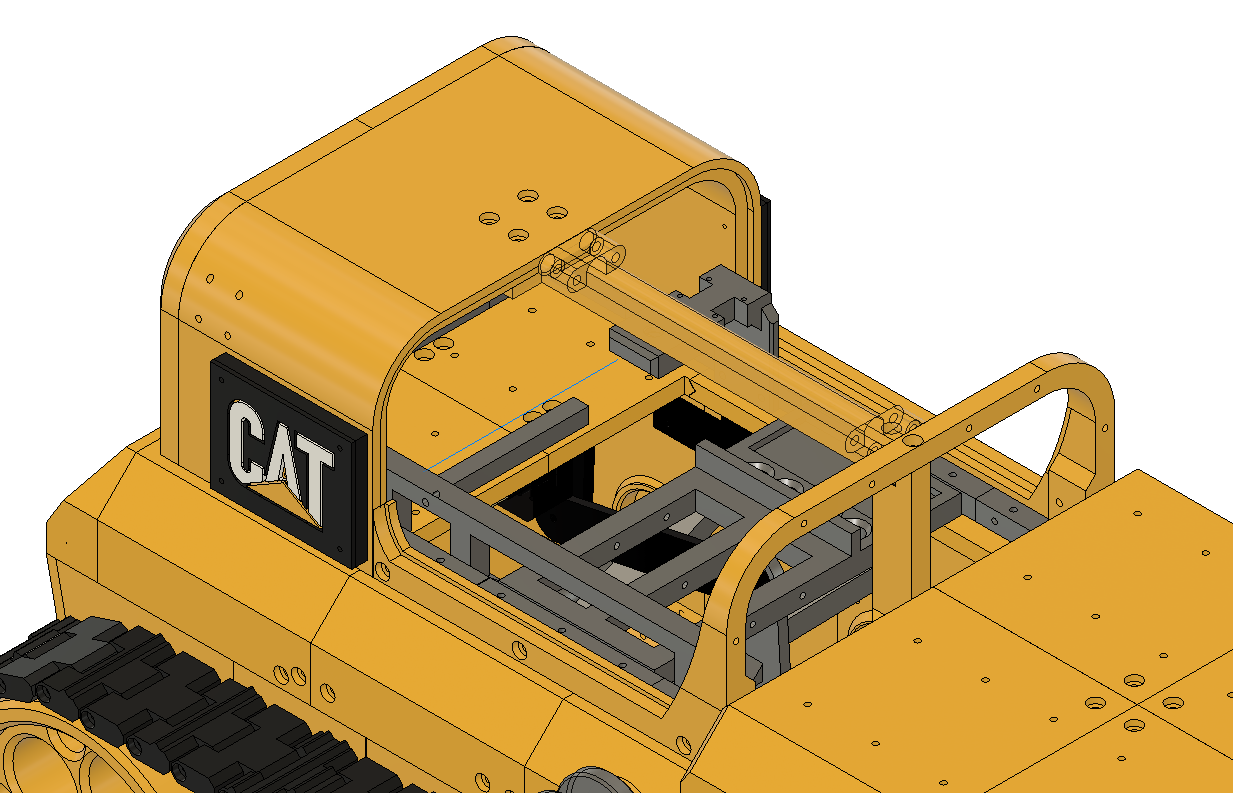
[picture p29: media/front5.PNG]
Front


Let's move on to the drivers cabine. Mount the "DriverCabBase" to the vehicle. Insert the LEDs 5/6 and 7/8 into the housings, again the lower numbered LEDs to the bottom, add the LED glasses and tops. Insert the LEDHouse 3 into the back left pocket of the "DriverCabBase", and LEDHouse 4 to the right pocket. Manage the cables. 

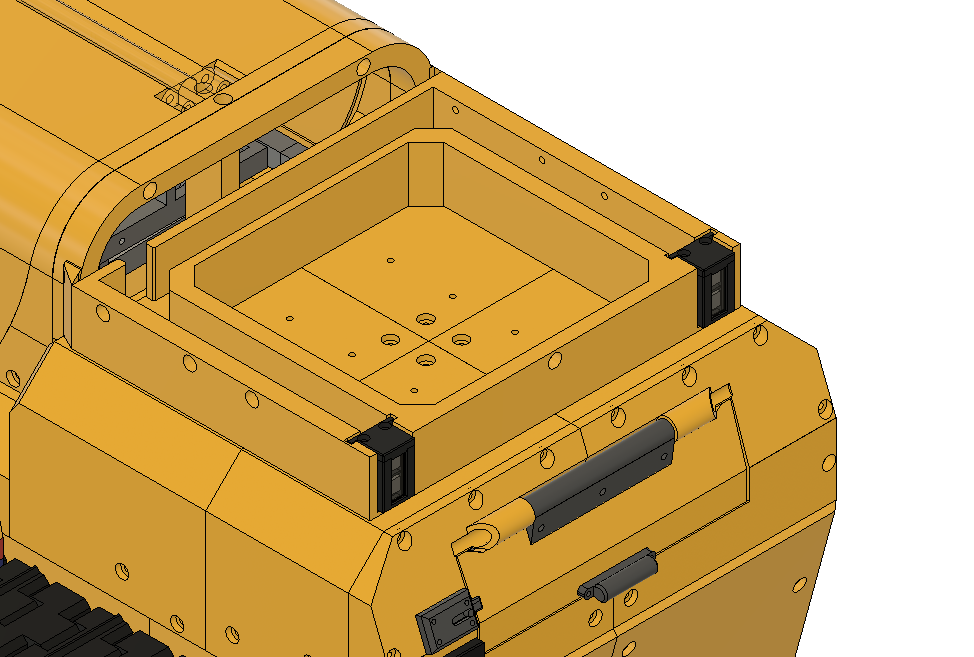
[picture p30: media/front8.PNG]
Front


Mount "DriverCabBack", "DriverCabFront" and "DriverCabRoofSupport". Fiddle the left LEDs through the hole of the rear right Cabine Support. Mount "DriversCabLowerTop" to the vehicle. 

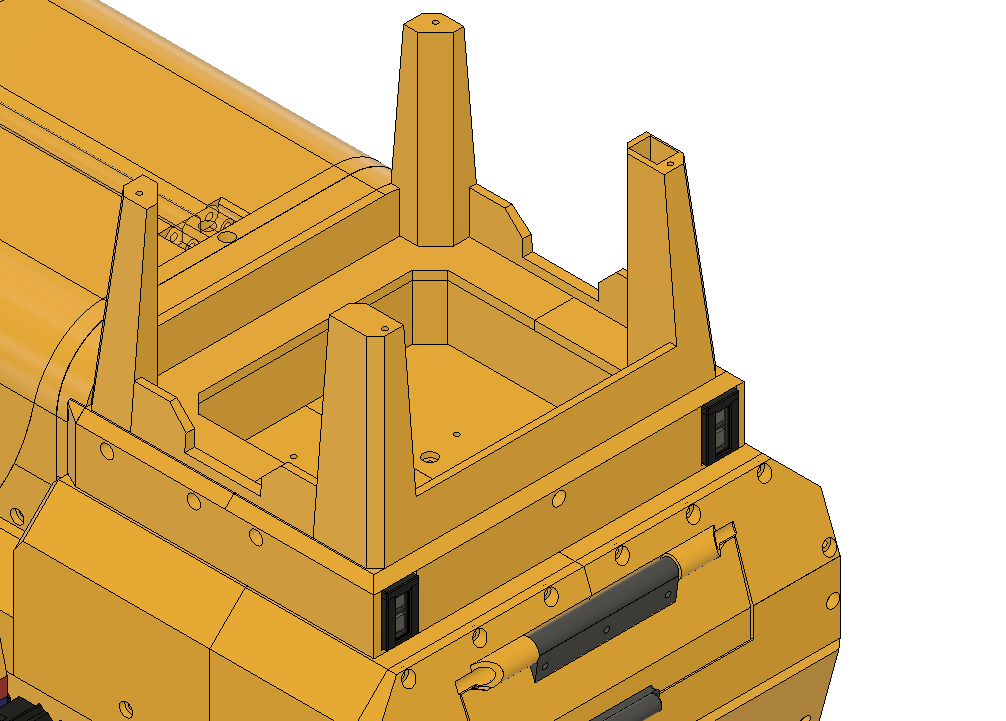
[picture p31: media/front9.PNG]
Front


Mount "StrobeHousing" to "DriversCabUpperTop". Fiddle the left LEDs through the hole. Insert the LEDs into the housing, by putting the cables between these 4 LED strips in the center of the housing. Mount the top the vehicle. Mount the "StrobeGlas" to the "StrobeHousing" using M2x8. The "Glas" has indexed holes, keep this in mind. 

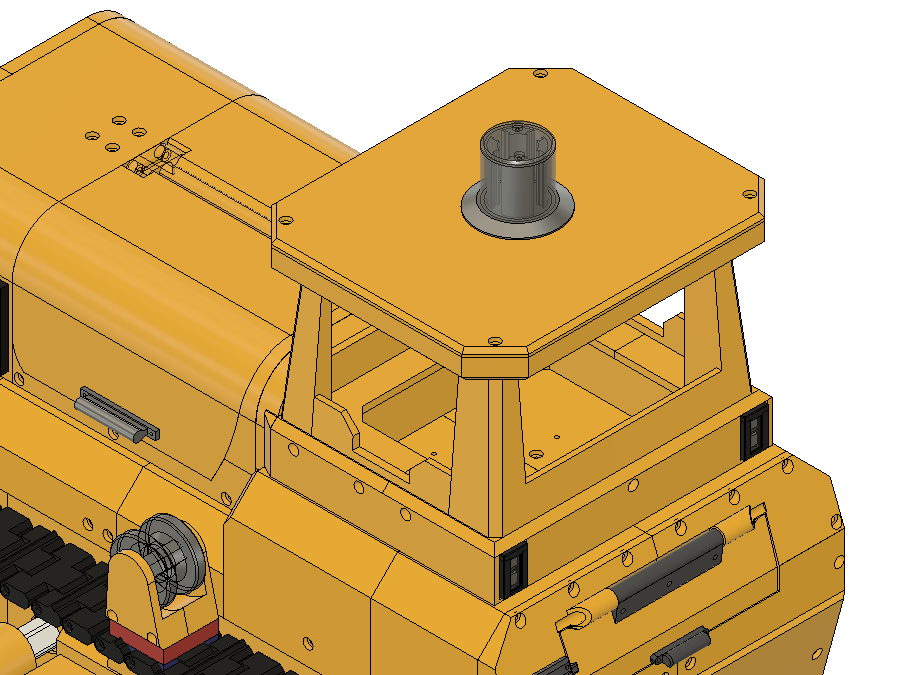
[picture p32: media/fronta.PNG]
Front


Now let's move on to the very last steps of our assembly, and therefore the finish line.

Before you mount the blade, you could of course take the opportunity to clear your candy stock, or you could drive around with your vehicle. To make sense of the light stuff, you would have to upload the arduino code to your Arduino first. However, it should beep if you drive forward/backward. On driving forward, the front light should be white, the backlight should be red. If you turn left or right the according LEDs should flash. The strobe should "turn" all the time. If you confused left or right during LED assembly, just change the numbers of the LED in your arduino sketch. Hint: You mighg have a hard time to plug the USB in and out of your Arduino. There are short Mini USB extension cables available. This cable will make your life easier.

Mount "BladeBarLeft" and "BladeBarRight" to the axles of your Blade servos. Fix them using some M3x20. Assemble the Blade now. "BladeLeft", "BladeMiddle" and "BladeRight" have holes for those M4 bolts. Insert them, and push the three Blade-parts together. Use screws to fix them at their backside. Add the "BladeEdge.." parts, using M2x8 screws. Mount "BladeHydraulicsHolderLeft" and "BladeHydraulicsHolderRight" to the blade. Mount "BladeHydraulicsGrillBaseLeft" and "BladeHydraulicsGrillBaseRight" to the "BonnetFront". Mount the "BladeHydraulicsTube" using "BladeHydraulicsClamp" to the "BladeHydraulicsGrillBase", make sure the tube is clamped around its half. Mount "BladeHydraulicsBolt" and "BladeHydraulicsBladeBase" together, twice. Mount these to the both "BladeHydraulicsHolder". Insert the "BladeHydraulicsBolt" into the Tubes.

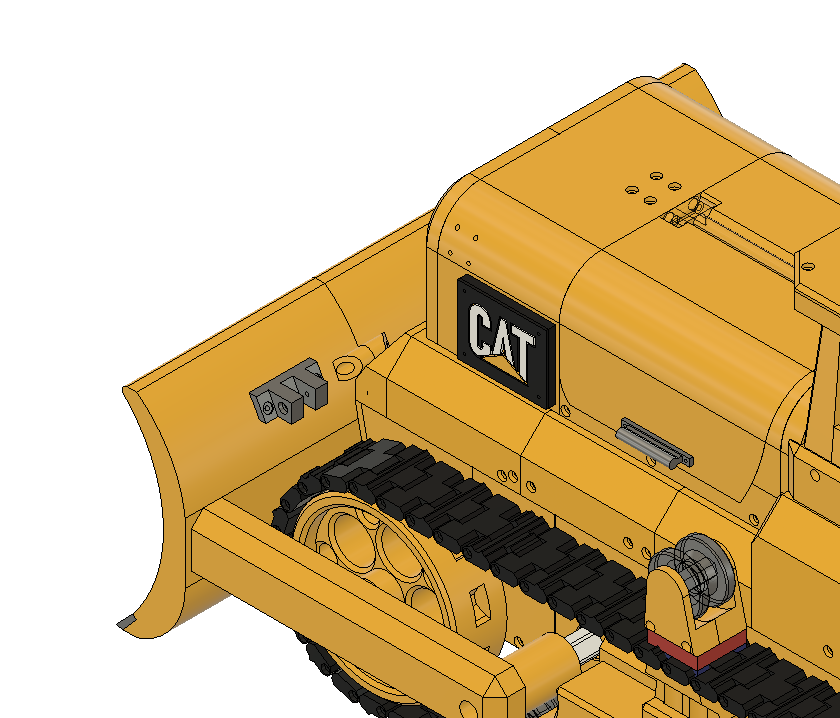
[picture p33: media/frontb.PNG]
Front


**Whoooohoooo! Done!**

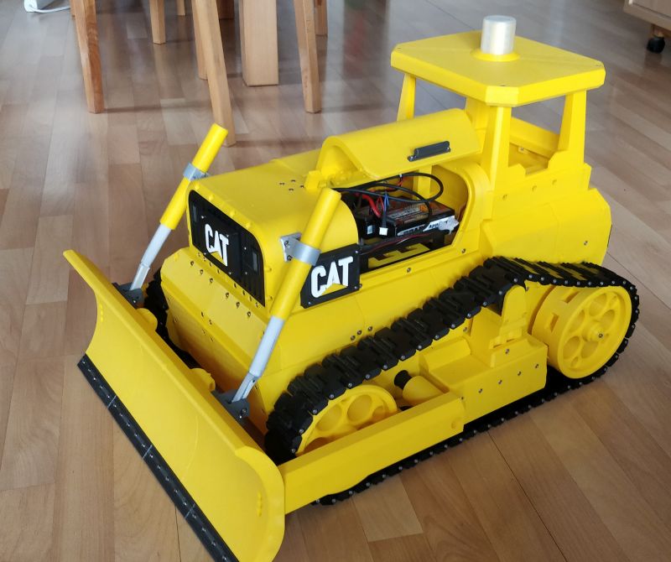
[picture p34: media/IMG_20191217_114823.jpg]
WHOOOOHOOOOO


## Who to thank?

I want to thank the guys of DasFilament.de and Prusa Research (https://www.prusa3d.com/). You deliver stuff that works out of the box. No hassle, no tinkering. Love it.

Thanks a lot to Brad, Aaron, Angelo and all others from Autodesk Fusion 360 (https://www.youtube.com/user/AutodeskFusion360), who deliver a lot of knowledge in their videos. Without these "another little trick" stuff I would have not been able to finish this project. Still, my CAD project contains a lot of crime - but nothing you could not hide behind 3d printed parts.

Thanks to the 3d maker noob "3DMN" aka Joe (https://twitter.com/3dmakernoob) and the 3d printing nerd "3DPN" aka Joel (https://twitter.com/joeltelling/) for their video channels, and the know how they collect with their communities. Finally it was Joe from 3DMN who awakened my interest in Arduino stuff - check out his mood lamp. Please consider becoming Patrons if you like their stuff, as I do.

Thanks to the guys of 3dSets.com, they hooked me up to the world of 3d printing RC vehicles with their Rancher, which is a much easier to assemble RC car compared to this bullozer. Easier to build? Yep, because of a comprehensive manual they deliver.

Thanks as well to my colleague Jumbo, who answered some of my questions with his endless electronics knowledge.

Thanks to the guys from OpenRCForums (https://openrcforums.com). They just delivered the perfect solution to a RC noob like I am. I gained so much knowledge during this conversation - appreciated.

Thanks to my family! They have hard times seeing me cursing, or being away for hours to do soldering stuff. Finally, they have to share the home with a guy who loves melting plastics to turn it into vehicles, drones and other stuff.

## Donation

I spent hours over hours doing this. And I love doing it, it is my hobby. I really like to provide you this stuff for free. You should not feel bad by just downloading the stuff and using it according to the Creative Commons License (4.0, BY / NC / SA). 

However, if you would like to spend me a coffee, you can use Paypal https://www.paypal.com/paypalme2/RedZoneAction - thanks in advance.

## Feedback

If you go for a build, I would like it very much to hear from you. Maybe you want to share pics of your Bulldozer? You can find me at

https://twitter.com/PjotrS72

https://www.prusaprinters.org/social/2411-pstimpel/prints

https://www.thingiverse.com/pstimpel

## Finally...

I am providing this stuff as it is. I do not promise anything, and I am not responsible for any harm you might create or receive by following this manual or by using the methods and results described in this manual.

### Warning

Lipo batteries can cause danger. Handle them carefully. If you create PCBs on your own pay attention and take security measurements when handling chemicals.

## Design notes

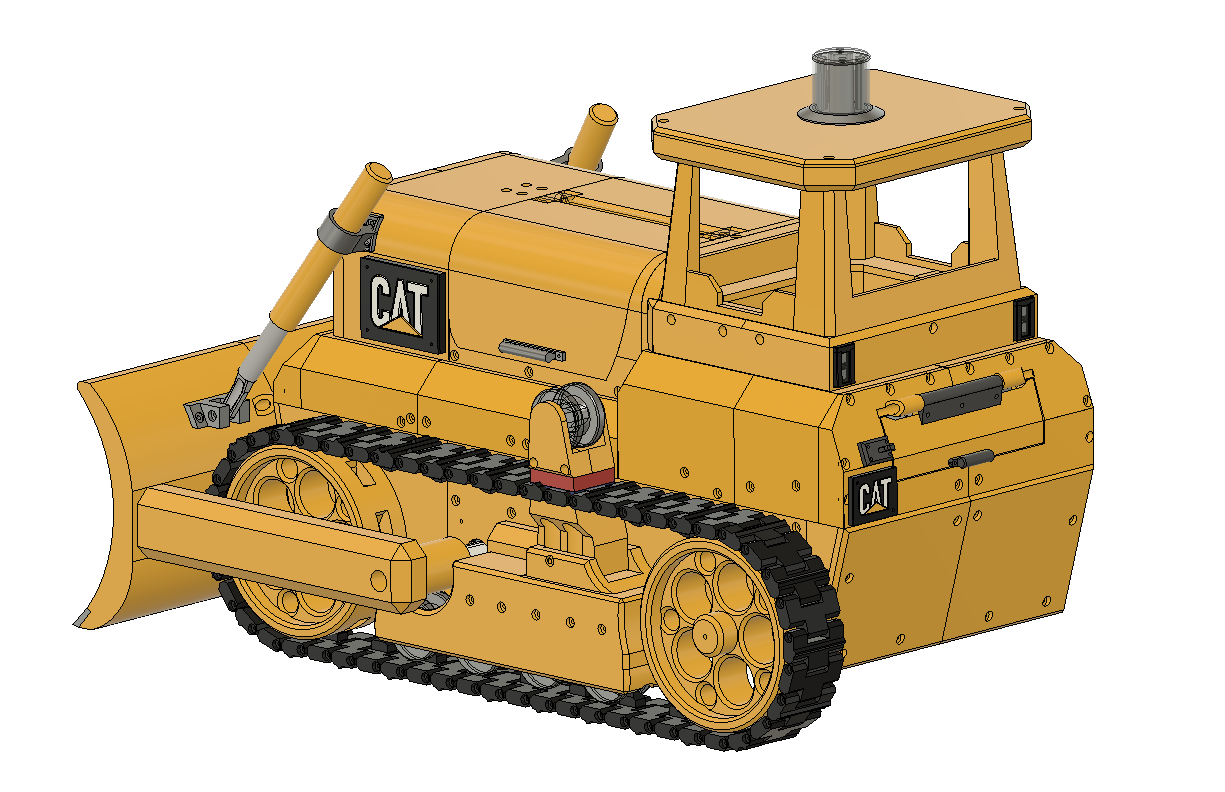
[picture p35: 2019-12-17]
media/full.PNG

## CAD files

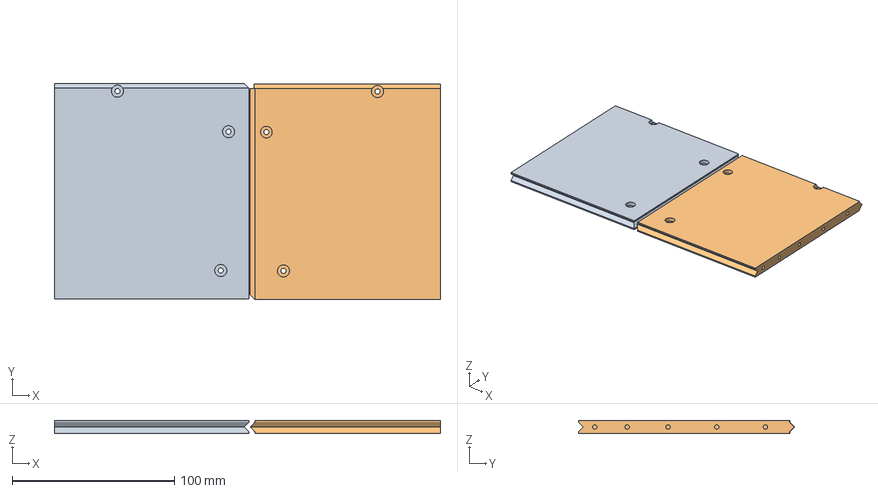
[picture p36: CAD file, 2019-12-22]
3mf-200x250/10_bottom3_yellow.3mf
237.9 x 133.2 x 8.00 mm
BottomLeft3.stl
BottomRight3.stl

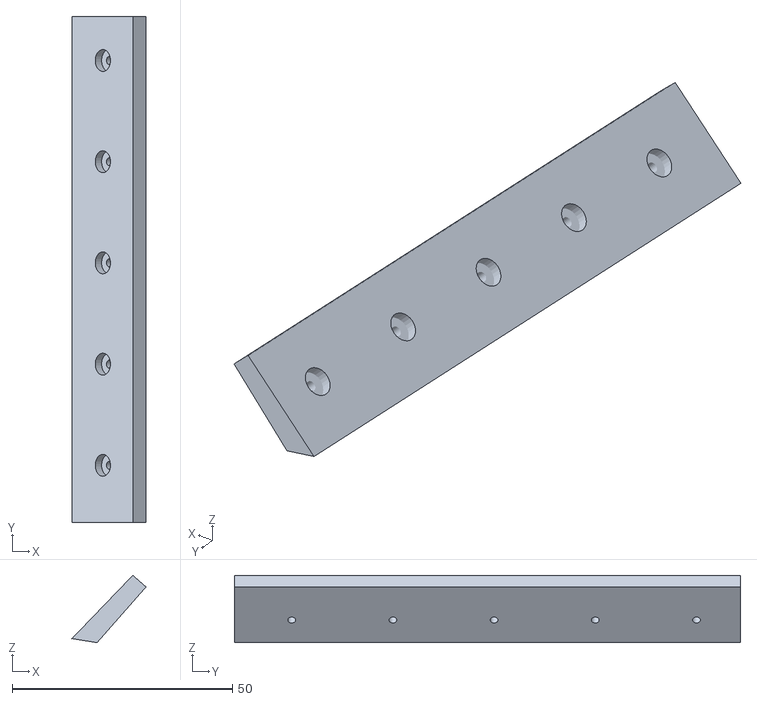
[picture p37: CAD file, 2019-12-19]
stl/Blade/BladeEdgeOuterRight.stl
16.8 x 115.0 x 15.3

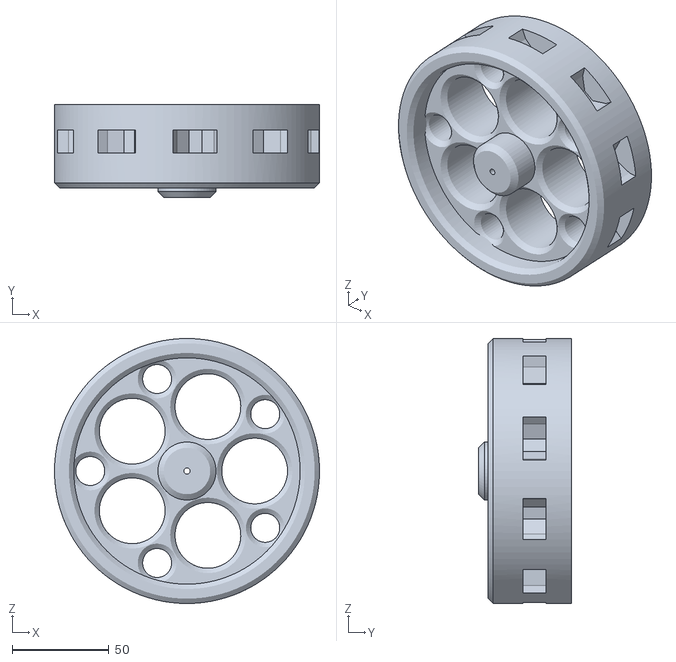
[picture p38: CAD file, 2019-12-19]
stl/Drive/Wheel.stl
137.0 x 48.0 x 137.0

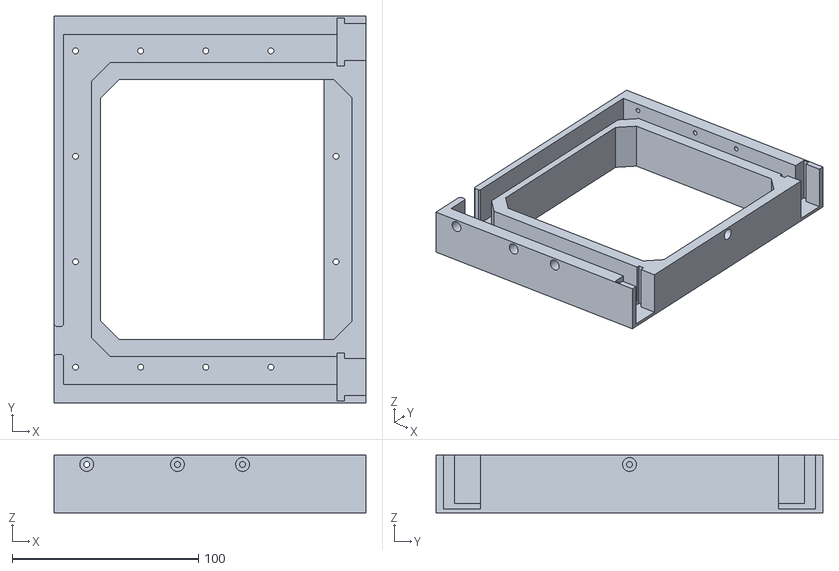
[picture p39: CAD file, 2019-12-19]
stl/DriverCab/DriverCabBase.stl
167.5 x 208.0 x 31.0

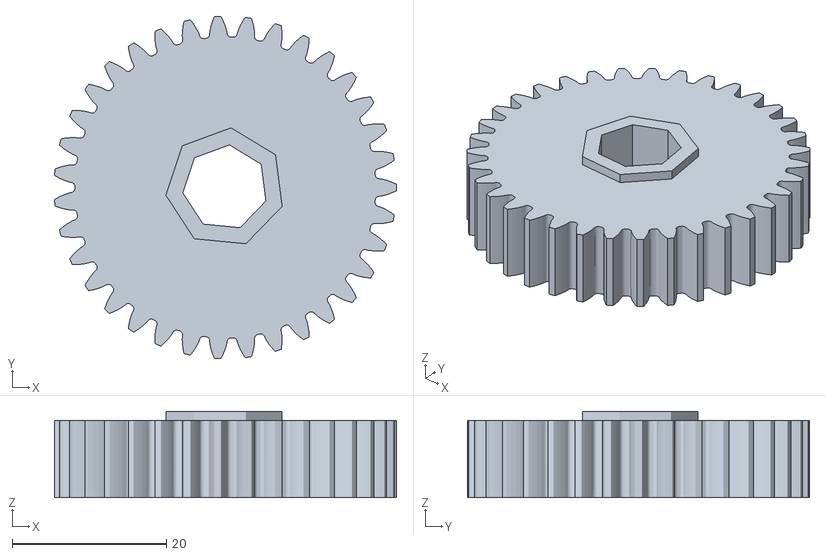
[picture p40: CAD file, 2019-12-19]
stl/Gearbox/BothSides/Gear1AxleA-7edges.stl
44.3 x 44.4 x 11.2

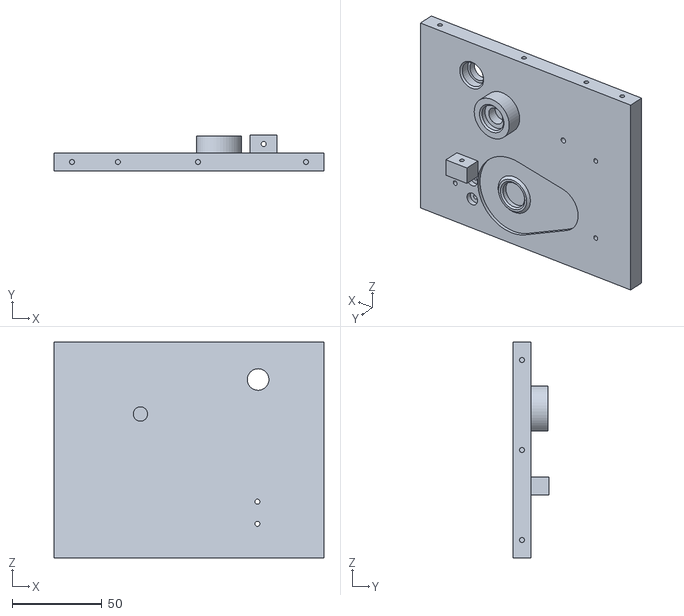
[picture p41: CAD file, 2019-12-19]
stl/Gearbox/Housing/GearhousingRight.stl
150.0 x 20.0 x 120.0

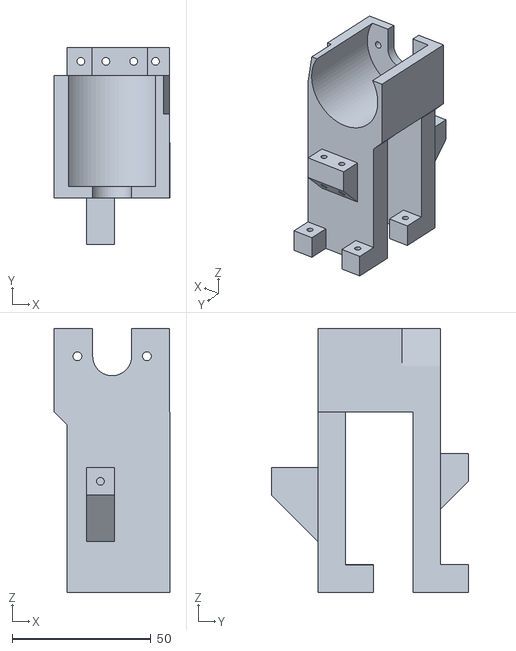
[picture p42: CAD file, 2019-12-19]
stl/Gearbox/LeftOnly/MotorstandLeft.stl
41.7 x 70.9 x 95.0

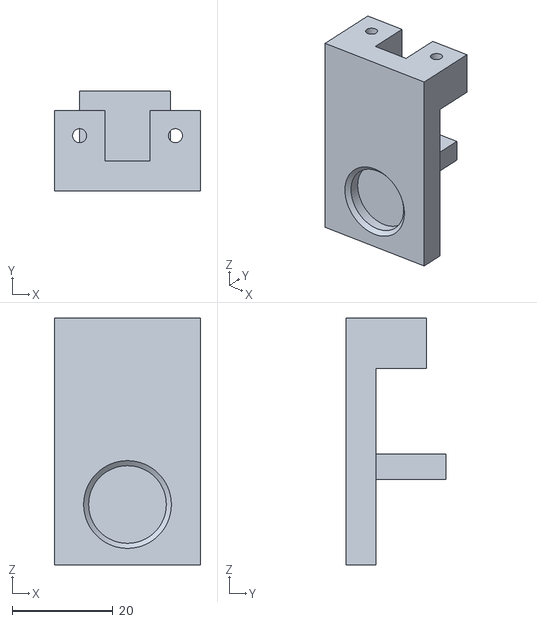
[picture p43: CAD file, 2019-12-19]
stl/Gearbox/RightOnly/GearboxBearingstandRightB.stl
29.0 x 19.9 x 49.0

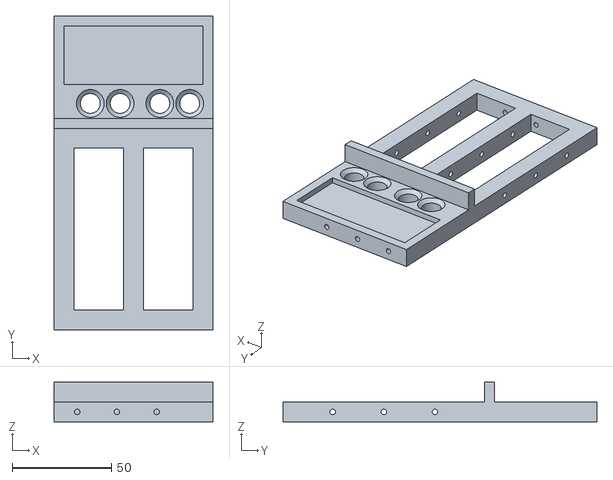
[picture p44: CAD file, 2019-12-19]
stl/Grill/ElectronicsESCBase.stl
80.0 x 158.0 x 20.0

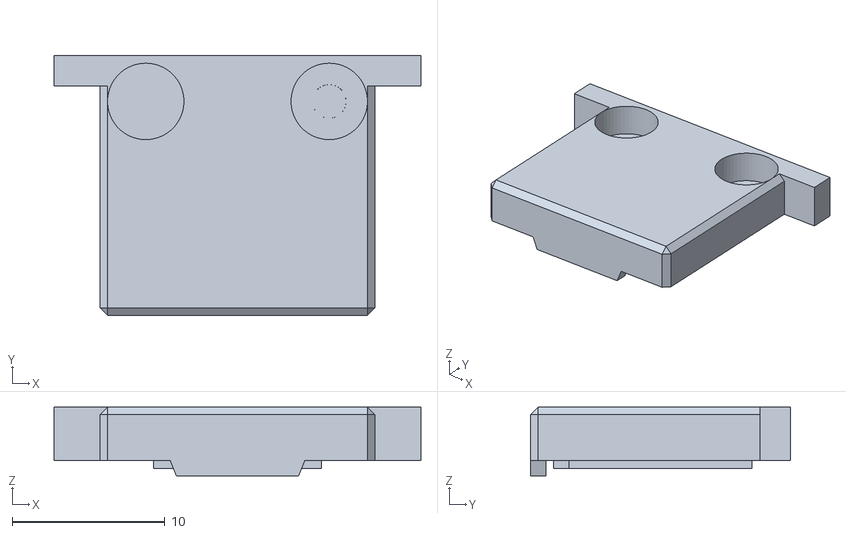
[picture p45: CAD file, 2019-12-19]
stl/LEDHousing/LEDTop.stl
24.0 x 17.0 x 4.50

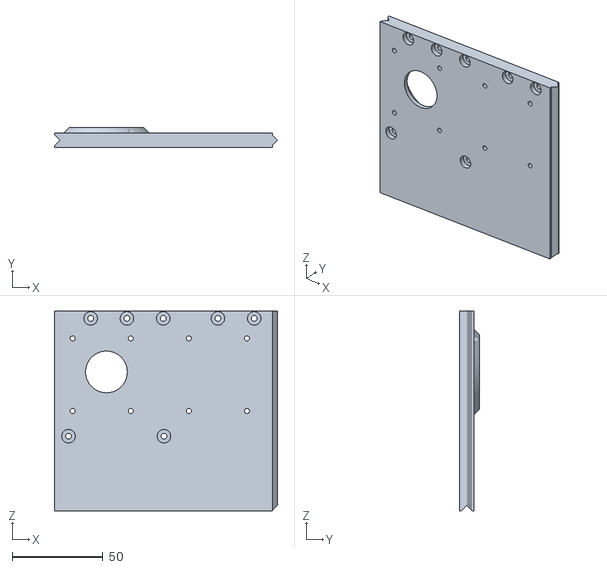
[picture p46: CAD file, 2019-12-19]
stl/LowerChassis/LowerChassisRight4.stl
122.8 x 11.0 x 110.0

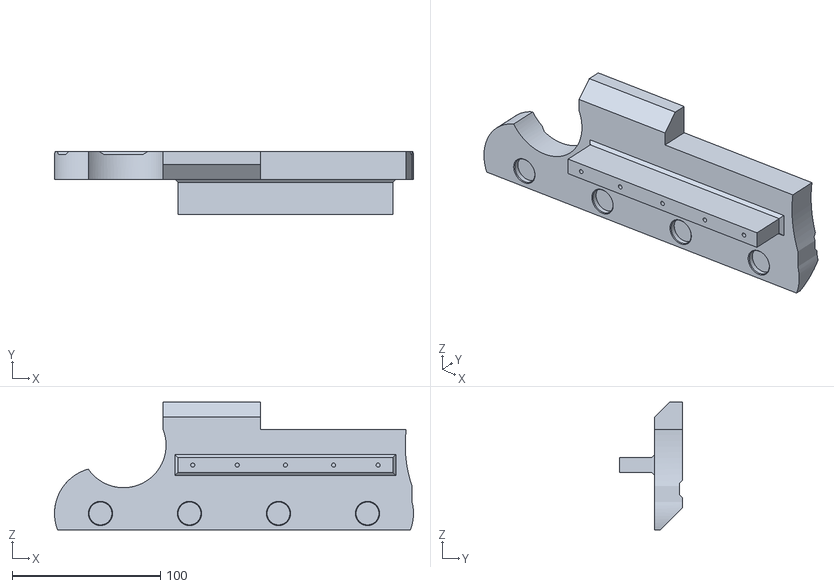
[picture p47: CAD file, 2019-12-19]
stl/Tracksupport/left/TrackSupportInnerLeft.stl
242.0 x 42.6 x 86.0

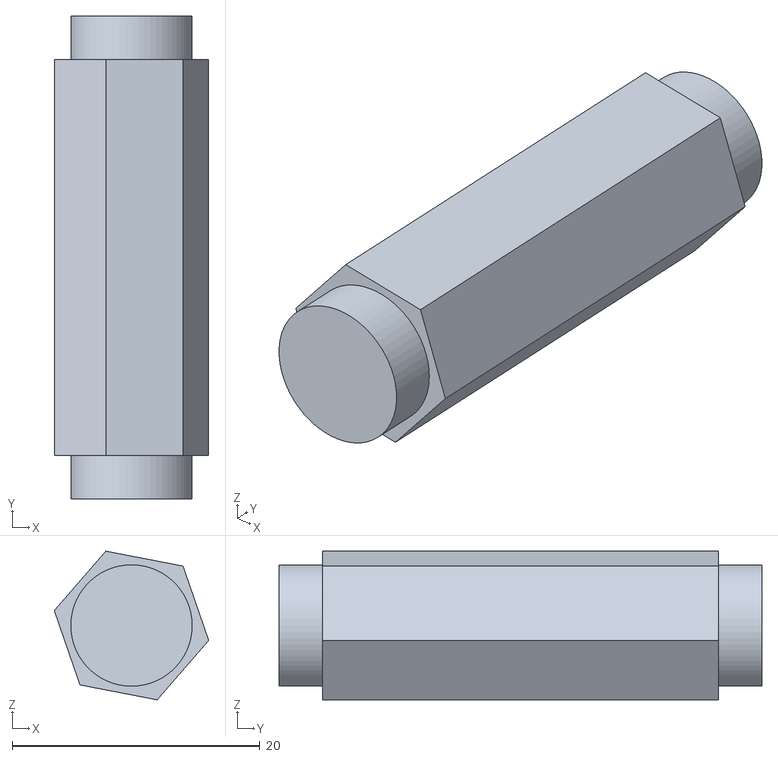
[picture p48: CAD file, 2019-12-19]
stl/Tracksupport/LowerSupportAxle.stl
12.5 x 39.0 x 12.0

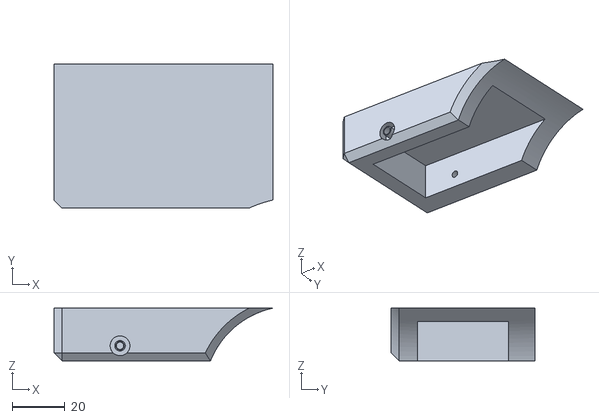
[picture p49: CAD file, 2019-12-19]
stl/Tracksupport/right/TensionMountRight.stl
82.9 x 54.5 x 20.0

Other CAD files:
stl/UpperChassis/LogoBackCover.stl
3mf-200x250/30_tracksupportaxles_nocolor.3mf
stl/Blade/BladeBarAxle.stl
stl/Drive/FrontAxle.stl
3mf-200x250/01_gears_nocolor.3mf
3mf-200x250/02_axles_nocolor.3mf
3mf-200x250/03_gearspacer_nocolor.3mf
3mf-200x250/04_gearsupports_nocolor.3mf
3mf-200x250/05_gearsupports2_nocolor.3mf
3mf-200x250/06_gearhousing_yellow.3mf
3mf-200x250/07_gearhousing2_yellow.3mf
3mf-200x250/08_bottom1_yellow.3mf
3mf-200x250/09_bottom2_yellow.3mf
3mf-200x250/11_bottom4_yellow.3mf
3mf-200x250/12_innersupport_nocolor.3mf
3mf-200x250/13_innersupport2_nocolor.3mf
3mf-200x250/14_lowerchassis1_yellow.3mf
3mf-200x250/15_lowerchassis2_yellow.3mf
3mf-200x250/16_lowerchassis3_yellow.3mf
3mf-200x250/17_lowerchassis4_yellow.3mf
3mf-200x250/18_lowerchassis5_yellow.3mf
3mf-200x250/19_lowerchassis6_yellow.3mf
3mf-200x250/20_axles_nocolor.3mf
3mf-200x250/21_axlesupport_nocolor.3mf
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

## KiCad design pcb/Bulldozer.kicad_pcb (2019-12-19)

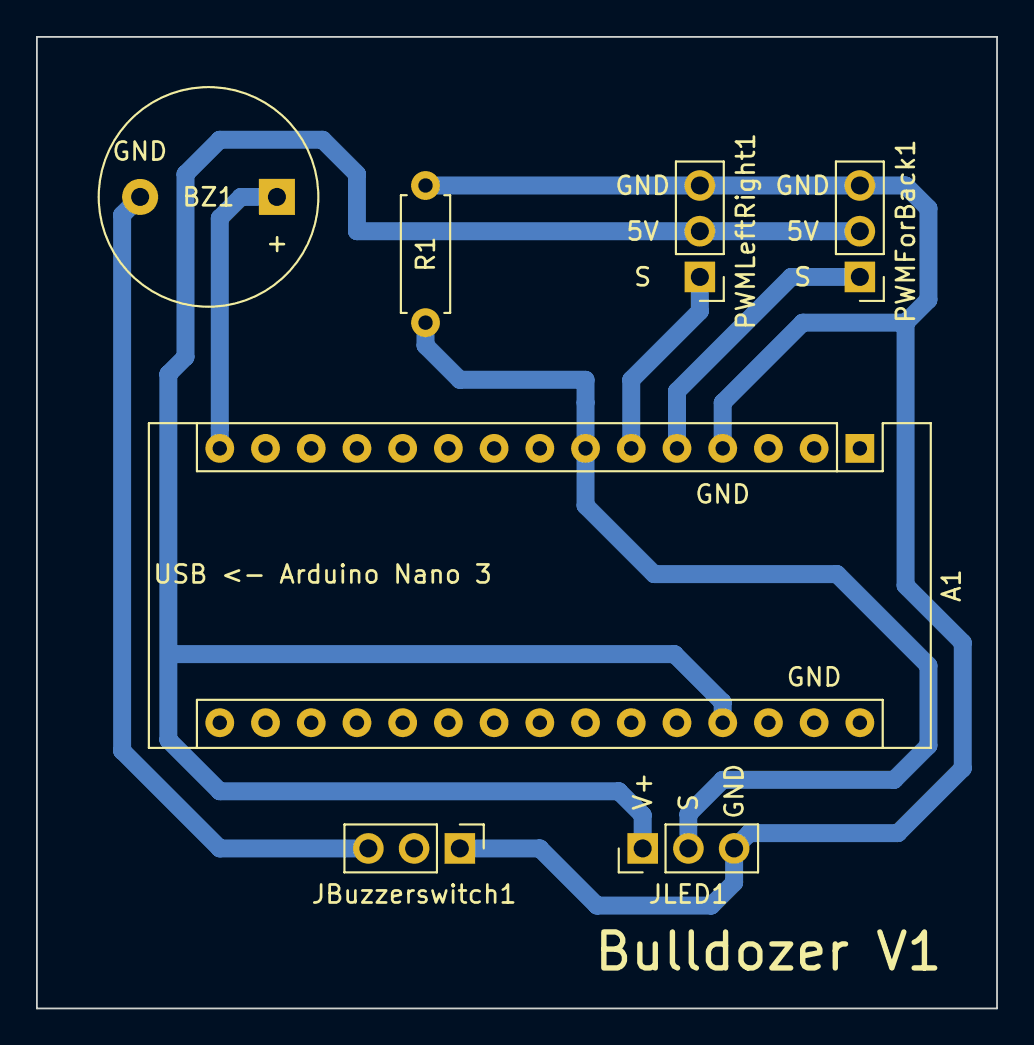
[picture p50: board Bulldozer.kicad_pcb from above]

Board: 2 copper layers, 53.3 x 54.0 mm, 7 parts (0 on the bottom side), 7 nets.

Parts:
A1: Arduino_Nano_v3.x; Arduino_Nano
BZ1: Buzzer; Buzzer_12x9.5RM7.6
JBuzzerswitch1: Conn_01x03; PinHeader_1x03_P2.54mm_Vertical
JLED1: Conn_01x03; PinHeader_1x03_P2.54mm_Vertical
PWMForBack1: Conn_01x03; PinHeader_1x03_P2.54mm_Vertical
PWMLeftRight1: Conn_01x03; PinHeader_1x03_P2.54mm_Vertical
R1: 270; R_Axial_DIN0207_L6.3mm_D2.5mm_P7.62mm_Horizontal

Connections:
unnamed: A1.5, PWMForBack1.1
unnamed: A1.6, PWMLeftRight1.1
unnamed: A1.7, JLED1.2, R1.2
unnamed: A1.15, BZ1.1
unnamed: A1.27, JLED1.1, PWMForBack1.2, PWMLeftRight1.2
unnamed: A1.4, A1.29, JBuzzerswitch1.1, JLED1.3, PWMForBack1.3, PWMLeftRight1.3, R1.1
unnamed: BZ1.2, JBuzzerswitch1.3

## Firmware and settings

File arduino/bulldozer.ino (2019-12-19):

#include <FastLED.h>

FASTLED_USING_NAMESPACE

#if defined(FASTLED_VERSION) && (FASTLED_VERSION < 3001000)
#warning "Requires FastLED 3.1 or later; check github for latest code."
#endif

#define DATA_PIN    4
#define LED_TYPE    WS2811
#define COLOR_ORDER GRB
#define NUM_LEDS    20
CRGB leds[NUM_LEDS];
#define FRAMES_PER_SECOND  120

volatile int pwm_value2 = 0;
volatile int old_pwm_value2 = 0;
volatile int prev_time2 = 0;
volatile int pwm_value3 = 0;
volatile int old_pwm_value3 = 0;
volatile int prev_time3 = 0;

volatile bool forward = false;
volatile bool oldforward = false;

volatile bool backward = false;
volatile bool oldbackward = false;

volatile bool left = false;
volatile bool oldleft=false;

volatile bool right = false;
volatile bool oldright = false;

volatile bool driving = false;
volatile bool olddriving = false;

volatile bool changeLED = false;

volatile int buzzercount=0;
int buzzerswitch=100;
int buzzerpin=12;

volatile int blinkercount=0;
int blinkerswitch = 1600;
volatile bool blinkerstate=false;
volatile bool oldblinkerstate=false;


volatile int strobecount=0;
int strobeswitch = 1250;
volatile int strobestate=0;
volatile int oldstrobestate=-1;

void setup() {
  Serial.begin(115200); //init debug console 

  // when pin D2 goes high, call the rising function
  attachInterrupt(0, rising2, RISING);

  // when pin D3 goes high, call the rising function
  attachInterrupt(1, rising3, RISING);

  pinMode(LED_BUILTIN, OUTPUT); //init built in LED

  Serial.print("go");

  pinMode(buzzerpin, OUTPUT);

  FastLED.addLeds<LED_TYPE,DATA_PIN,COLOR_ORDER>(leds, NUM_LEDS).setCorrection(TypicalLEDStrip);
  FastLED.setBrightness(200);
  
}
 
void loop() {
  if(driving) {
    //Serial.print(" ° ");  
  } else {
    //Serial.print("   ");
  }
  if(left) {
    //Serial.print(" < ");  
  } else if(right) {
    //Serial.print(" > ");
  } else {
    //Serial.print(" - ");
  }
  if(forward) {
    //Serial.print(" ^ ");  
  } else if(backward) {
    //Serial.print(" v ");
  }
  Serial.println(" :");

  changeLED=false;
  if(olddriving != driving) {
    changeLED=true;
    olddriving = driving;
  }
  
  if(oldforward != forward) {
    changeLED=true;
    oldforward = forward;
  }

  if(oldbackward != backward) {
    changeLED=true;
    oldbackward = backward;
  }

  if(oldleft != left) {
    changeLED=true;
    oldleft = left;
  }

  if(oldright != right) {
    changeLED=true;
    oldright = right;
  }
  
  if(left || right) {
    blinkercount++;
    if(blinkercount>(blinkerswitch*2)) {
      blinkerstate=false;
      blinkercount=0;
      if(blinkerstate != oldblinkerstate) {
        oldblinkerstate=false;
        blinkerstate=false;
        changeLED=true;
        //Serial.println("blinker off");
      }
    } else {
      if(blinkercount>(blinkerswitch)) {
        blinkerstate=true;
        if(blinkerstate != oldblinkerstate) {
          oldblinkerstate=true;
          blinkerstate=true;
          changeLED=true;
        //Serial.println("blinker on");
        }
      }
    }
  } else {
    blinkercount=0;
  }

  strobecount++;
  //Serial.print(strobecount);
  //Serial.print("-");
  //Serial.print(oldstrobestate);
  //Serial.print("-");
  //Serial.println(strobestate);
  
  if(strobecount<= strobeswitch) {
    //Serial.println("A");
    strobestate=1;
    if(strobestate!=oldstrobestate) {
      
      oldstrobestate=strobestate;
      leds[8]=CRGB::Yellow;
      leds[9]=CRGB::Yellow;
      leds[10]=CRGB::Yellow;
      leds[11]=CRGB::Yellow;
      leds[12]=CRGB::Yellow;
      leds[13]=CRGB::Yellow;
      leds[14]=CRGB::Black;
      leds[15]=CRGB::Black;
      leds[16]=CRGB::Black;
      leds[17]=CRGB::Black;
      leds[18]=CRGB::Black;
      leds[19]=CRGB::Black;
      
      changeLED=true;
      //Serial.println("changeto1");
    }
    
  } else if(strobecount > strobeswitch && strobecount <= (strobeswitch*2)) {
    //Serial.println("B");
    strobestate=2;
    if(strobestate!=oldstrobestate) {
      
      oldstrobestate=strobestate;
       leds[8]=CRGB::Black;
      leds[9]=CRGB::Black;
      leds[10]=CRGB::Black;
      leds[11]=CRGB::Yellow;
      leds[12]=CRGB::Yellow;
      leds[13]=CRGB::Yellow;
      leds[14]=CRGB::Yellow;
      leds[15]=CRGB::Yellow;
      leds[16]=CRGB::Yellow;
      leds[17]=CRGB::Black;
      leds[18]=CRGB::Black;
      leds[19]=CRGB::Black;
      
      changeLED=true;
      //Serial.println("changeto2");
    }
    
  } else if(strobecount > (strobeswitch*2) && strobecount <= (strobeswitch*3)) {
    //Serial.println("C");
    strobestate=3;
    if(strobestate!=oldstrobestate) {
      
      oldstrobestate=strobestate;
       leds[8]=CRGB::Black;
      leds[9]=CRGB::Black;
      leds[10]=CRGB::Black;
      leds[11]=CRGB::Black;
      leds[12]=CRGB::Black;
      leds[13]=CRGB::Black;
      leds[14]=CRGB::Yellow;
      leds[15]=CRGB::Yellow;
      leds[16]=CRGB::Yellow;
      leds[17]=CRGB::Yellow;
      leds[18]=CRGB::Yellow;
      leds[19]=CRGB::Yellow;
      
      changeLED=true;
      //Serial.println("changeto3");
    }
    
  } else if(strobecount > (strobeswitch*3) && strobecount <= (strobeswitch*4)) {
    //Serial.println("D");
    strobestate=4;
    if(strobestate!=oldstrobestate) {
      
      oldstrobestate=strobestate;
       leds[8]=CRGB::Yellow;
      leds[9]=CRGB::Yellow;
      leds[10]=CRGB::Yellow;
      leds[11]=CRGB::Black;
      leds[12]=CRGB::Black;
      leds[13]=CRGB::Black;
      leds[14]=CRGB::Black;
      leds[15]=CRGB::Black;
      leds[16]=CRGB::Black;
      leds[17]=CRGB::Yellow;
      leds[18]=CRGB::Yellow;
      leds[19]=CRGB::Yellow;
      
      changeLED=true;
      //Serial.println("changeto4");
    }
    
  } else {
    strobestate=-1;
    strobecount=0;
    //Serial.println("reset");
  }
    
  if(driving) {
    buzzercount++;
    if(buzzercount>(buzzerswitch*250)) {
      buzzercount=0;
      digitalWrite(buzzerpin, LOW);
      //Serial.println("led off");
    } else if(buzzercount>(buzzerswitch*125)) {
      digitalWrite(buzzerpin, LOW);
      //Serial.println("led off");
       
    } else {
      if(buzzercount>(buzzerswitch)) {
        digitalWrite(buzzerpin, HIGH);
        //Serial.println("led on");
      }
    }
  } else {
    digitalWrite(buzzerpin, LOW);
  }
  //Serial.println(buzzercount);
  //reset
  //for( int i = 0; i < NUM_LEDS; i++) {
    //leds[i] = CRGB::Blue;
  //}

//0 front left scheinwerfer
//1 front left blinker
//2 front right scheinwerfer
//3 front right blinker
//4 back left scheinwerfer/rücklicht
//5 back left blinker
//6 back right scheinwerfer/rücklicht
//7 back right blinker
//8-19 Strobe ligh, 4 groups 3 leds each. 8-10 group 1, 11-13 group 2, 14-16 group 3, 17-19 group 4
  
  if(left && blinkerstate) {
     leds[1]=CRGB::Orange;
     leds[5]=CRGB::Orange;
     
  }
  if(left && !blinkerstate) {
     leds[1]=CRGB::Black;
     leds[5]=CRGB::Black;
     
  }
  if(right && blinkerstate) {
     leds[3]=CRGB::Orange;
     leds[7]=CRGB::Orange;
     
  }
  if(right && !blinkerstate) {
     leds[3]=CRGB::Black;
     leds[7]=CRGB::Black;
     
  }
  if(!left && !right) {
    leds[1]=CRGB::Black;
    leds[5]=CRGB::Black;
    leds[3]=CRGB::Black;
    leds[7]=CRGB::Black;
    oldblinkerstate=false;
    blinkerstate=false; 
  }

  if(!backward) {
    leds[0] = CRGB::White;
    leds[2] = CRGB::White;
    leds[4] = CRGB::Red;
    leds[6] = CRGB::Red;
    
  }

  if(backward) {
    leds[0] = CRGB::Yellow;
    leds[2] = CRGB::Yellow;
    leds[4] = CRGB::White;
    leds[6] = CRGB::White;
    
  }

  if(changeLED) {
    FastLED.show();  
    FastLED.delay(1000/FRAMES_PER_SECOND); 
  }

}
 
void rising2() {
  attachInterrupt(0, falling2, FALLING);
  prev_time2 = micros();
}

void rising3() {
  attachInterrupt(1, falling3, FALLING);
  prev_time3 = micros();
}
 
void falling2() {
  attachInterrupt(0, rising2, RISING);
  pwm_value2 = micros()-prev_time2; //calculate PWN from input

  //if change is big enough, forward it to servo
  if((pwm_value2 - old_pwm_value2) > 50 or (pwm_value2 - old_pwm_value2) < -50) {
    //Serial.print("--IN2: ");
    //Serial.println(pwm_value2);
    //delay(50);                          // give the servo some time to reach desired position
    old_pwm_value2 = pwm_value2;          //store new value in old_pwm_value
    //digitalWrite(LED_BUILTIN, HIGH);   // turn the LED on (HIGH is the voltage level)
    //delay(50);                       // wait
    //digitalWrite(LED_BUILTIN, LOW);     //turn led off

    if(pwm_value2> 1550) {
      driving=true;
      forward=true;
      backward=false;
    }
    
    if(pwm_value2< 1450) {
      driving=true;
      forward=false;
      backward=true;
    }

    if(pwm_value2<= 1550 && pwm_value2>= 1450) {
      driving=false;
      forward=false;
      backward=false;
    }
    
  } else {
    //the change was between -50 and 50, this is not enough to forward it to output
    //Serial.print("too low for a change: ");
    //Serial.println(pwm_value);
   }
  
}

void falling3() {
  attachInterrupt(1, rising3, RISING);
  pwm_value3 = micros()-prev_time3; //calculate PWN from input

  //if change is big enough, forward it to servo
  if((pwm_value3 - old_pwm_value3) > 50 or (pwm_value3 - old_pwm_value3) < -50) {
    //Serial.print("++IN3: ");
    //Serial.println(pwm_value3);
    //delay(50);                          // give the servo some time to reach desired position
    old_pwm_value3 = pwm_value3;          //store new value in old_pwm_value
    //digitalWrite(LED_BUILTIN, HIGH);   // turn the LED on (HIGH is the voltage level)
    //delay(50);                       // wait
    //digitalWrite(LED_BUILTIN, LOW);     //turn led off

    if(pwm_value3< 1700) {
      left=true;
      right=false;
    }
    
    if(pwm_value3> 1300) {
      left=false;
      right=true;
    }

    if(pwm_value3<= 1700 && pwm_value3>= 1300) {
      left=false;
      right=false;
    }
  } else {
    //the change was between -50 and 50, this is not enough to forward it to output
    //Serial.print("too low for a change: ");
    //Serial.println(pwm_value);
   }
  
}

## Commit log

2019-12-19 STLs added
    [BladeBarAxle.stl, BladeBarBearingHolderLeft.stl, BladeBarBearingHolderRight.stl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]
2019-12-19 Add Arduino sketch Add PCB layout file
    [Bulldozer.kicad_pcb]
2019-12-22 Added 3mf files for more convenience Bugfix in README Bugifx in naming convention of stl file Gearbox/Housing/GearboxStandLeftUpper
    [01_gears_nocolor.3mf, 02_axles_nocolor.3mf, 03_gearspacer_nocolor.3mf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]
